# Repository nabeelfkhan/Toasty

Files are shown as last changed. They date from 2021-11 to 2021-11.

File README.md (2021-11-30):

# Toasty

Meet Toasty: The Brave Little Toaster Oven

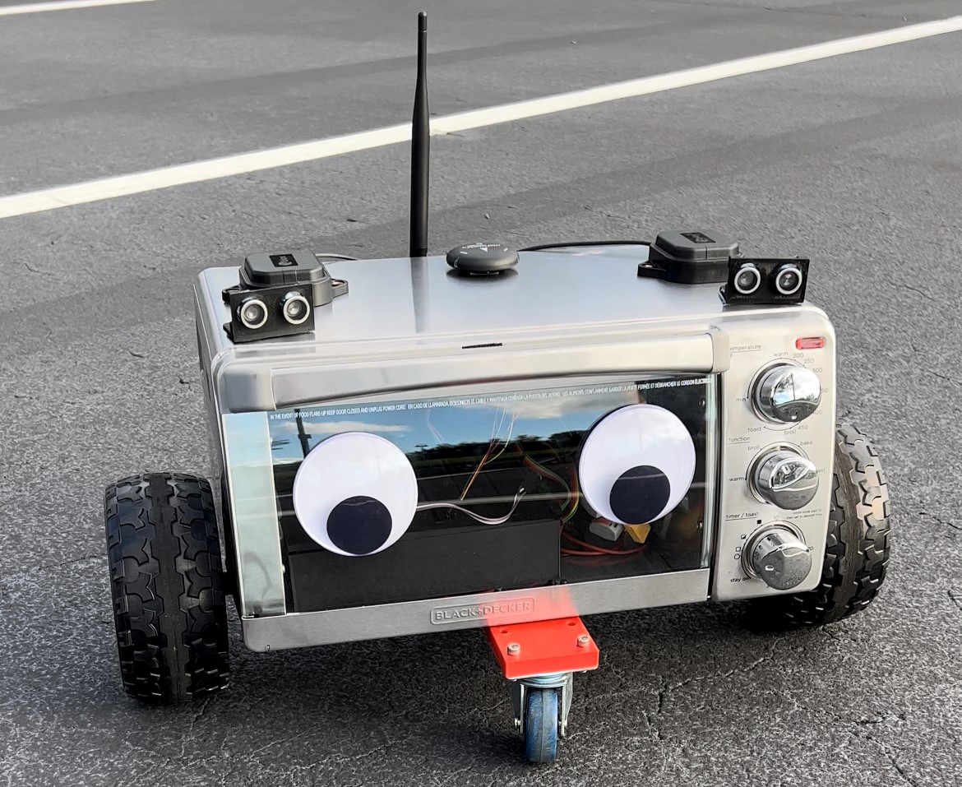
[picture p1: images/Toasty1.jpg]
Toasty
  
<p align="center">
  animated 
</p>

Toasty is an affordable DIY autonomous robotics research platform.  

**Disclaimer: The motors used in this project are dangerously powerful. Follow this guide at your own risk. Follow all local laws and regulations for autonomous and remote control vehicles. Test and make configuration changes in an open area away from obstacles, and always maintain line of sight.**

My long term goal is for Toasty to serve as a long range delivery robot with obstacle avoidance. In the near term, I'm experimenting wtith PointPerfect SSR GNSS corrections from u-blox to achieve cm level accuracy.

Pre-fabricated robotics platforms that can carry heavy loads over long distances are quite expensive. Cost effective Motors, Motor Controllers, and Frames are tough to find. Toasty is a budget and eco-friendly alternative, leveraging recycled materials and the following projects:

For brushless motor control, I referenced the excellent work of lucysrausch in hacking a hoverboard as a cost effective brushless motor solution.
Hoverboards are quite powerful. Most are capable of supporting 200 lbs (90kg) with a top speed of 25 mph (40km/h) and up to 10 miles (16 km) of range with some reprogramming.  
https://github.com/lucysrausch/hoverboard-firmware-hack  
Her repo also contains some examples of projects others have created using hacked hoverboards.  

EFeru further modified this code base to include FOC control, offering smoother control and higher speeds.  
https://github.com/EFeru/hoverboard-firmware-hack-FOC  

Randy Mackay's contributions to ArduRover made this project a breeze. Configuring Ardupilot for rover use is documented in detail on the official website.
Link to his YouTube channel with some tutorials:  
https://www.youtube.com/channel/UCm393BzMOyRPUo8MtKp5alg  

The best part of using these components is that minimal programming and configuration is needed to get started.

Hoverboards are out of style and sell for pennies on the dollar on ebay, craigslist, and facebook marketplace. I regularly find listings for $30 boards.
How can you beat a 10S Protected 4.4Ah 36V battery pack with a Charger, Battery Management System, two brushless 350W motors, and a frame capable of carrying 200lbs (90kg)?

The toaster oven is a sturdy aluminum enclosure that requires only basic tools to teardown and modify. You can find these used for $10-15. 
Aluminum extrusions just aren't as fun.

## Bill of Materials:

| Item  | Estimated Cost | Vendor
| --- | --- | --- |
| **Minimum BOM for RC control** |  | 
| Hoverboard | $20-60 | Plenty of used products on FB Marketplace, Craigslist, Ebay, etc.
| Toaster Oven |  $15 | Plenty of used products on FB Marketplace, Craigslist, Ebay, etc.
| Several 3D Printed mounts and enclosures (STL files included in repo) |  $5 | /3D_Prints
| 2x 2in Swivel Casters| $5 | https://www.harborfreight.com/material-handling/tires-casters/swivel-casters/2-inch-x-7-8-eighth-inch-light-duty-swivel-caster-41518.html  |
| RC Receiver for manual control and Arming (FS-iA6B)  | $12 | AliExpress, Amazon
| RC Controller or PS4 controller for manual control (FS-i6X)  | $40 | AliExpress, Amazon
| **Required for autonomous operation** |  |
| Ardupilot compatible flight controller w/ GNSS,Compass | $45-200+ | I used a Pixhawk 4 mini from Sparkfun. I can't vouch for the boards from AliExpress, but there are some lower cost options available. More options available here: https://ardupilot.org/rover/docs/common-autopilots.html#common-autopilotsSparkfun
| Telemetry Radio (BLE or SubGhz)  | $20 | Sparkfun, Amazon, Ebay
| **Optional for enhanced autonomous functions** |  |
| u-blox ZED-F9P/F9R High Precision GNSS Receiver (ZED-F9R also integrates Dead Reckoning)  | $150+ | Future, Digikey, Holybro, Ardusimple, Sparkfun
| Ultrasonic Sensors  | $10 | Sparkfun, Amazon, Ebay
| Cellular Modem for remote control  | $65+ | Sparkfun, Hologram
| Lidar or ToF camera  | TBD | TBD
| Raspberry Pi | $30 | https://www.raspberrypi.com/products/raspberry-pi-4-model-b/

## Block Diagram
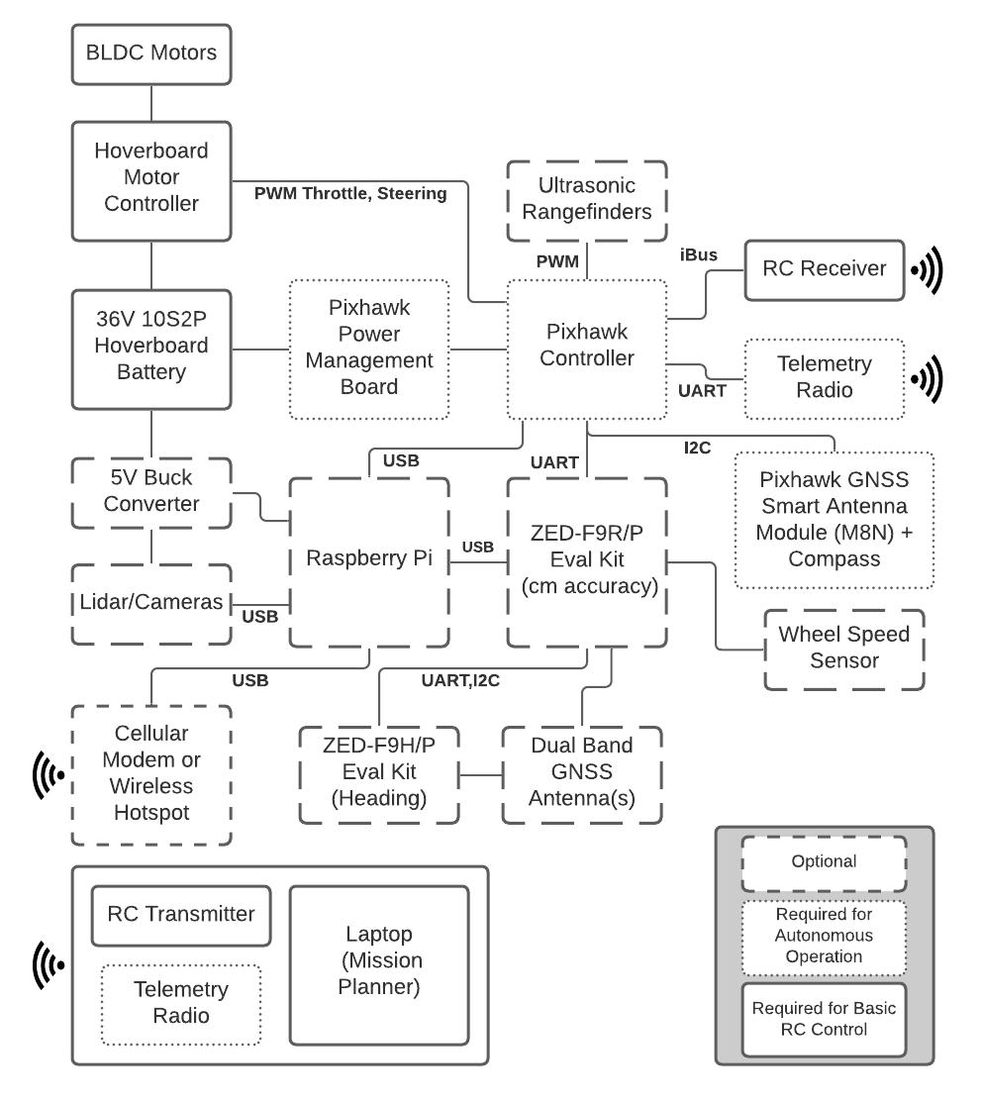
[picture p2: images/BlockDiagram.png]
Block Diagram
  

## Build

Here is an outline of the steps I followed using a Pixhawk 4 mini, Ardupilot,  and a hacked hoverboard. Depending on your choice of controller, you may need to make some modifications.

**Step 1**: Disassemble your hoverboard and Follow instructions on Feru's repo to flash the MCU. Make sure you pick the appropriate input. If you are using Ardupilot like me, select PWM input  
https://github.com/EFeru/hoverboard-firmware-hack-FOC  

**Step 2**: Mount the motors to the toaster frame. I used the mounts that came with my hoverboard, which required a couple 3D printed spacers. You may need to get a little creative here, as hoverboard mounts have different geometries and some may require more effort to combine with the toaster frame.
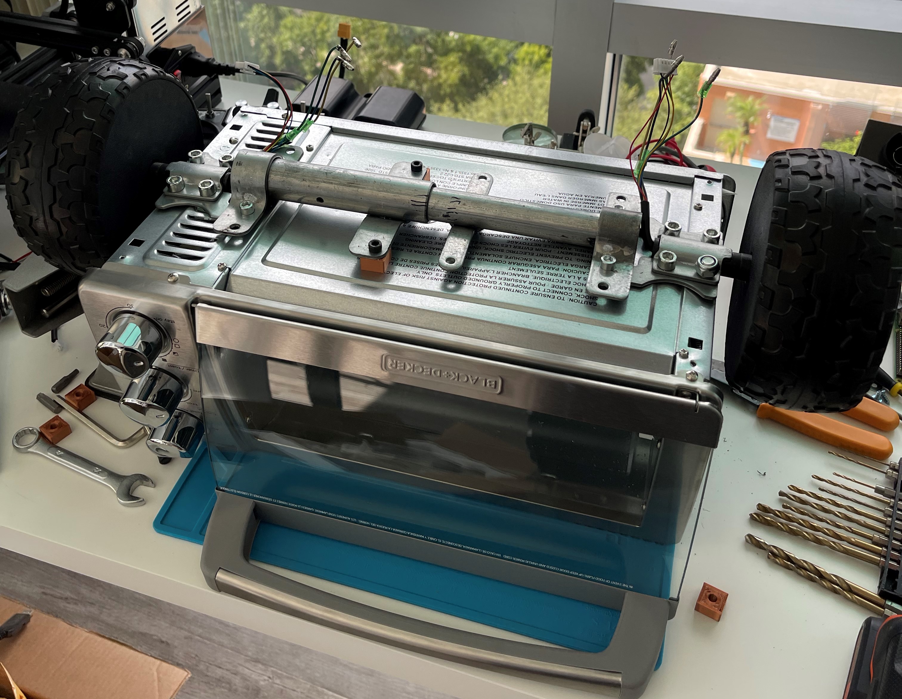
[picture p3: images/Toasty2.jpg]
Toasty
 

**Step 3**: Wire up the motor controller as shown in the block diagram. I 3D printed a few enclosures and mounts for the electronics. See /3D_Prints. I also crimped some custom dupont connector cables to interface between the motor controller and hall sensor cables.
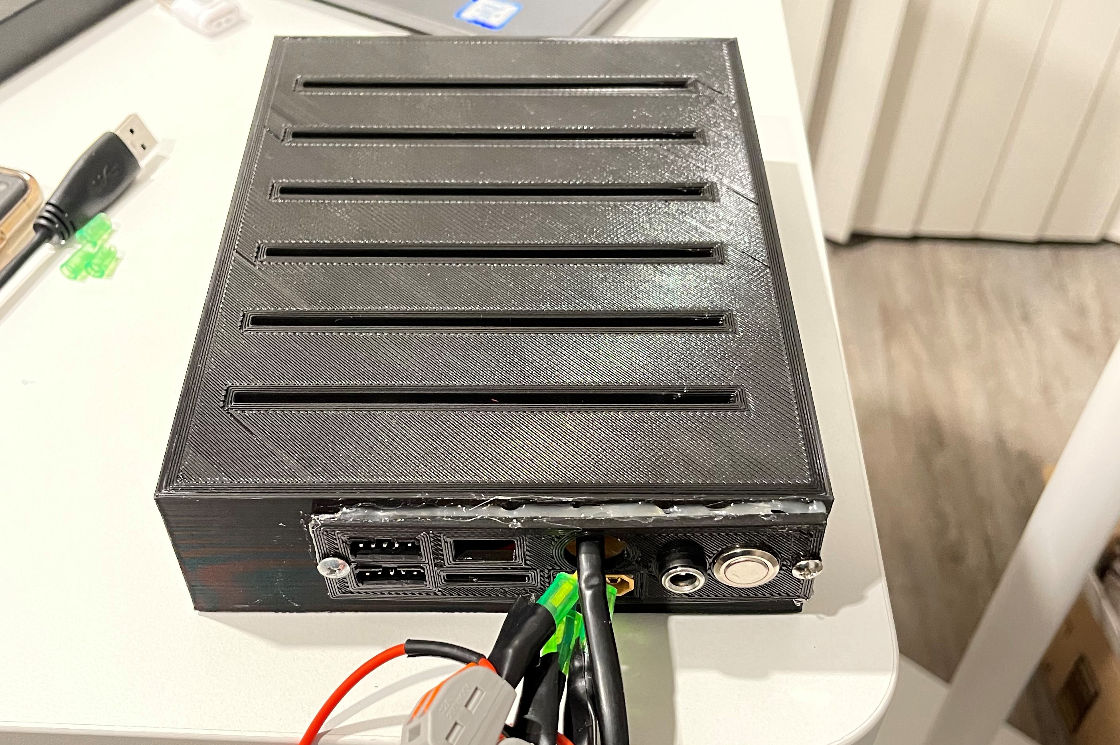
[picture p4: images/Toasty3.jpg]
Toasty
 

**Step 4**: Test with an RC receiver - Channels 0,1 can be connected directly to the hoverboard motor controller using Pin x for speed and pin x for steering. Place toasty on an elevated surface so the wheels can move freely and ensure throttle and steering are functioning as expected.
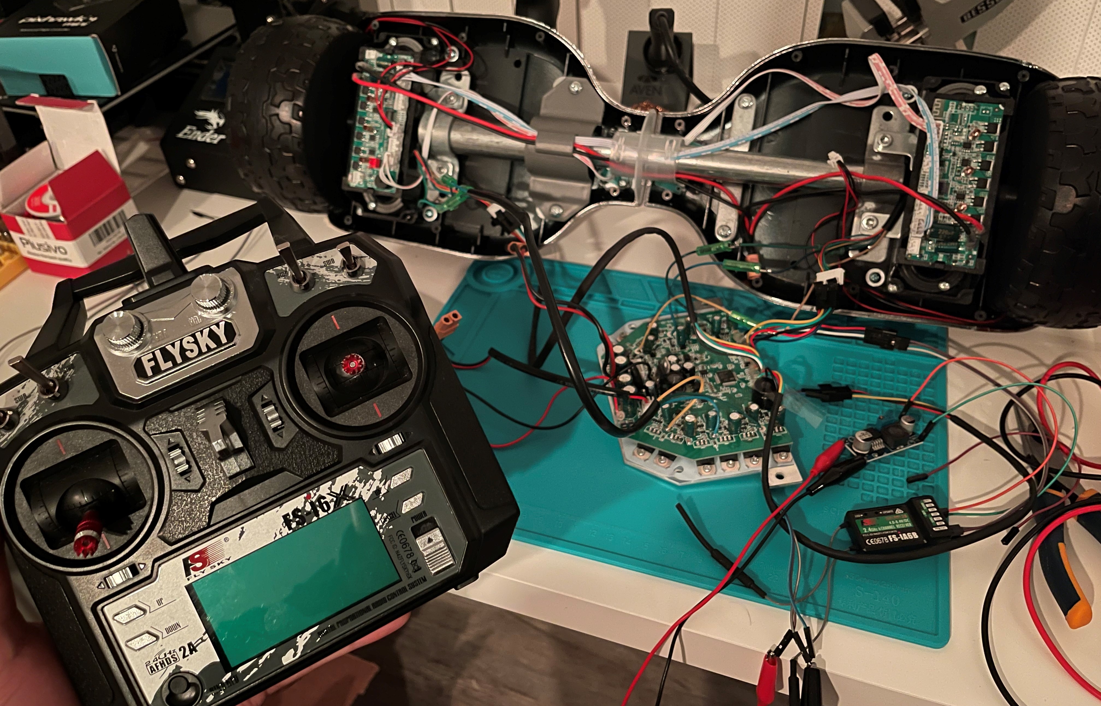
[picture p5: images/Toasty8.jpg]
Toasty
 

**Step 5**: Follow the Ardupoilot Rover steps outlined here: https://ardupilot.org/rover/docs/gettit.html  

**Step 6**: Connect the Pixhawk to the motor controller as shown on the block diagram. I've uploaded a 3D printed mount for the pixhawk in the repo. For convenience, I used velcro to secure the device to the top of the oven compartment.
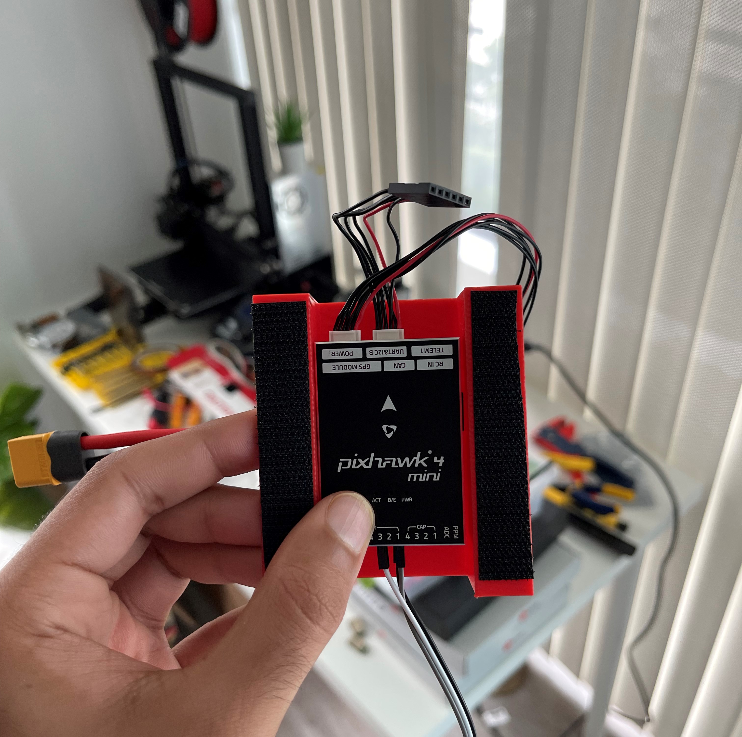
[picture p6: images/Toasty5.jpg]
Toasty
 
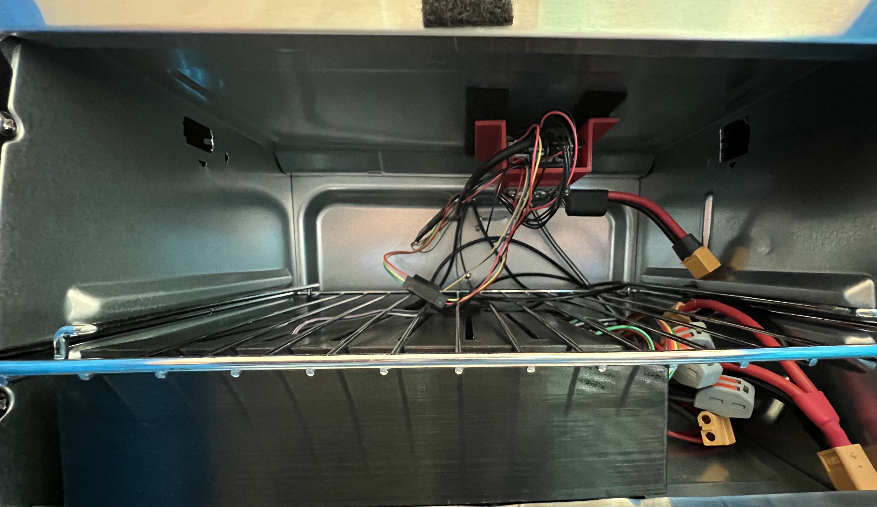
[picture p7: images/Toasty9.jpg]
Toasty
 

**Step 7**: Place Toasty on an elevated surface again to safely perform some motor tests. At this stage you should have already performed the RC controller calibration and set the rover to mode x. You're ready to go on your first mission!
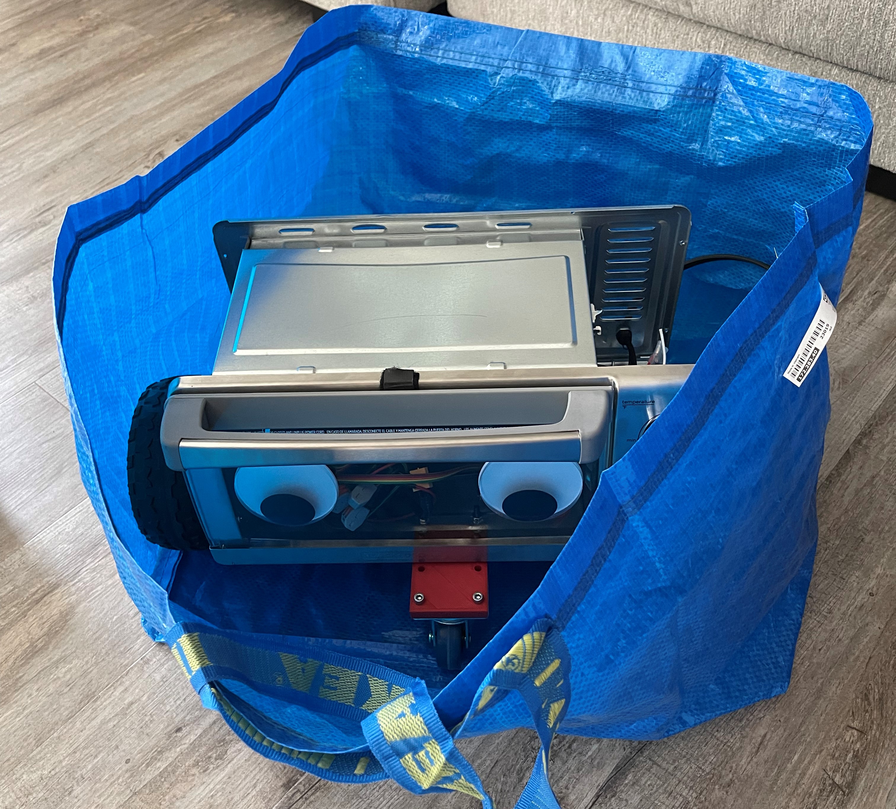
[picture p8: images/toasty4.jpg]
Toasty
 

**Step 8**: Test manual control and follow tuning steps as outlined in Randy's videos here:

https://www.youtube.com/watch?v=mV9Dxp1PX-8  
https://www.youtube.com/watch?v=9zOlvTsHY6k  

**Step 9**: Configure ardupilot to prioritize the appropriate external GNSS. Set up and calibrate magnetometers, and object avoidance sensors. Details are outlined in the ardupilot rover documentation: 

https://ardupilot.org/rover/docs/common-gps-for-yaw.html  
https://ardupilot.org/rover/docs/common-object-avoidance-landing-page.html  

Toasty 
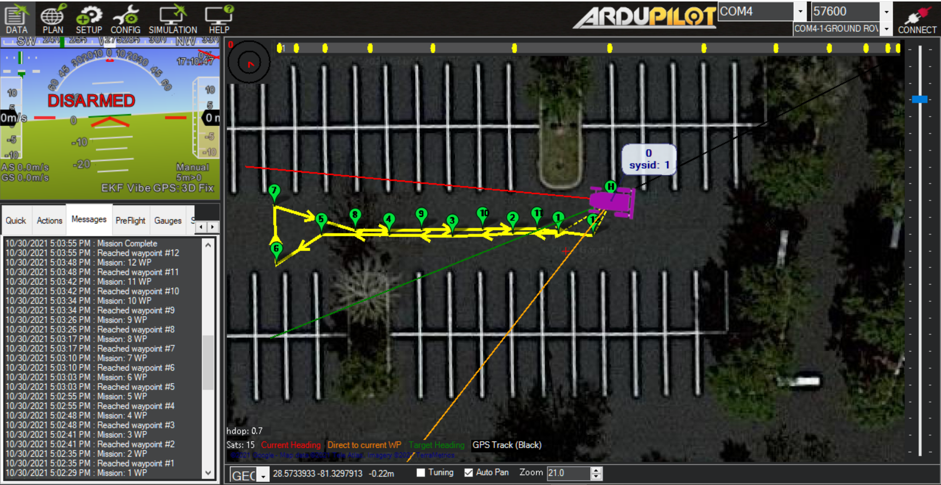
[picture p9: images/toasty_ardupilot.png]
Toasty
 

## Tips

- Configure maximum setpoints for throttle and steering if using Ardupilot. Toasty can and will spin out of control if you don't...

## To do:
Add obscacle avoidance via Lidar, ToF camera  
Include ROS node for indoor navigation.  
Migrate to Jetson Nano.  

## Links:
https://github.com/pixhawk/Hardware/blob/master/FMUv5/Pixhawk4-Pinouts.pdf  
https://www.thingiverse.com/thing:100486

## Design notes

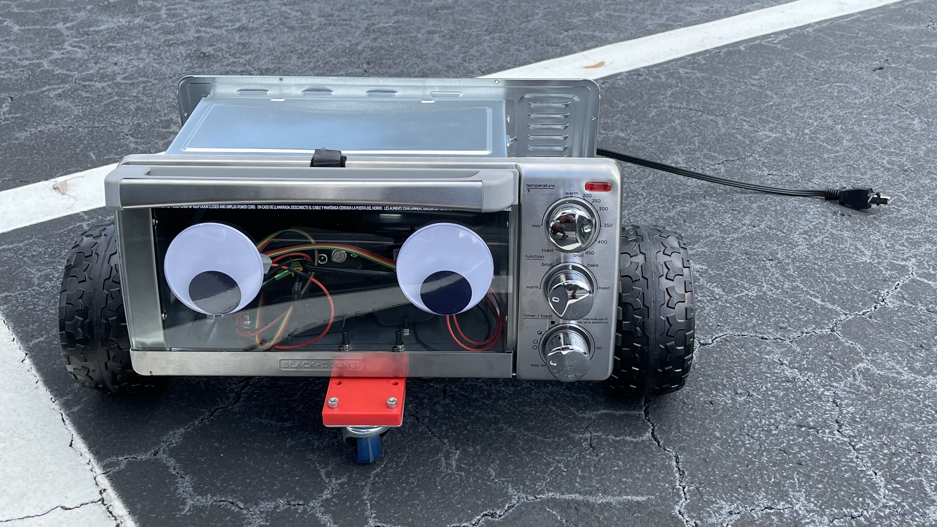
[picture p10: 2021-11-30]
images/toasty.jpg

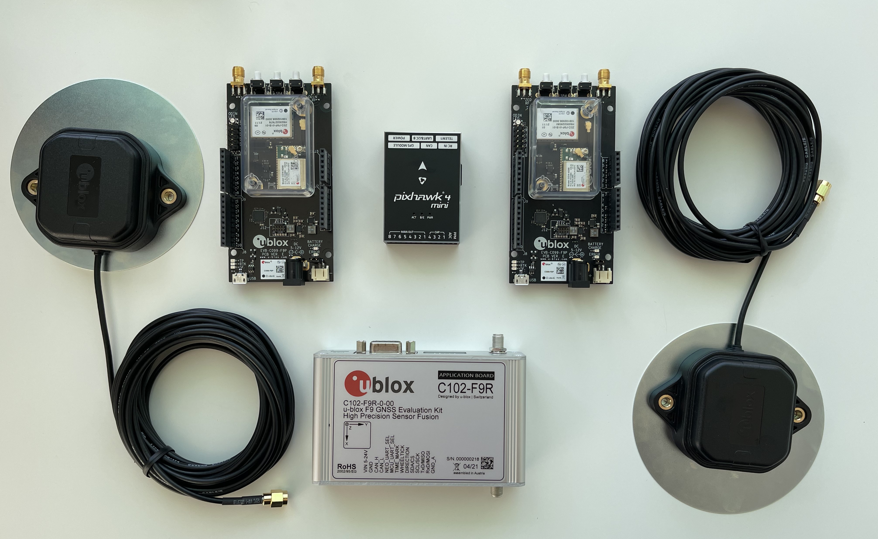
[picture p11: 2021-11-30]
images/Toasty7.jpg

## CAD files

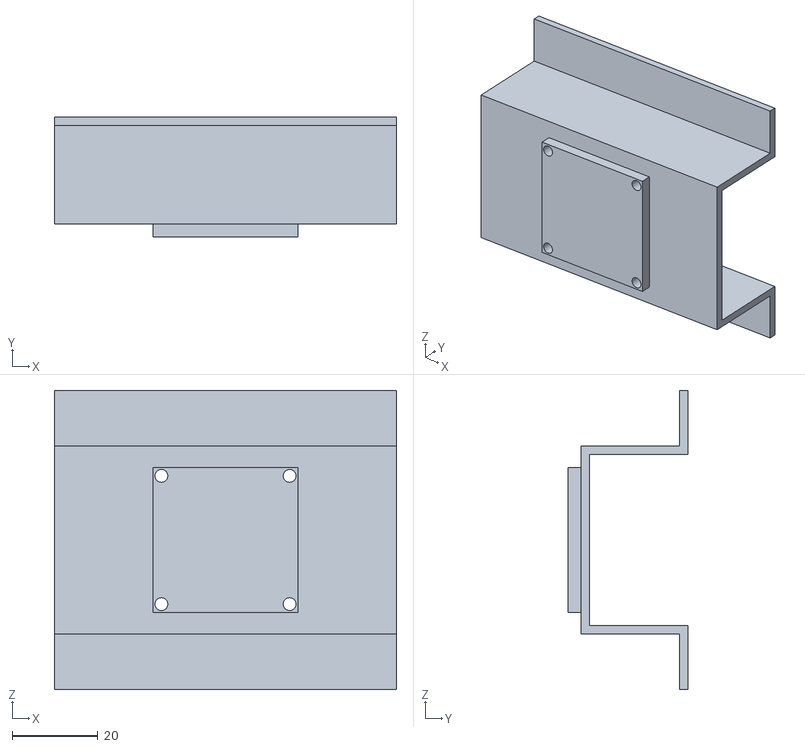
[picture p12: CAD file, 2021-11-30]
3D_Prints/px4holder.stl
80.0 x 28.0 x 70.0

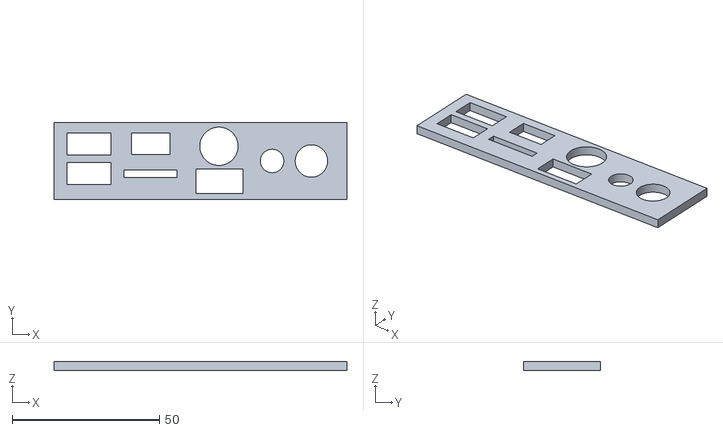
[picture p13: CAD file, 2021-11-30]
3D_Prints/esc_body_iopanel.stl
99.5 x 26.0 x 3.00

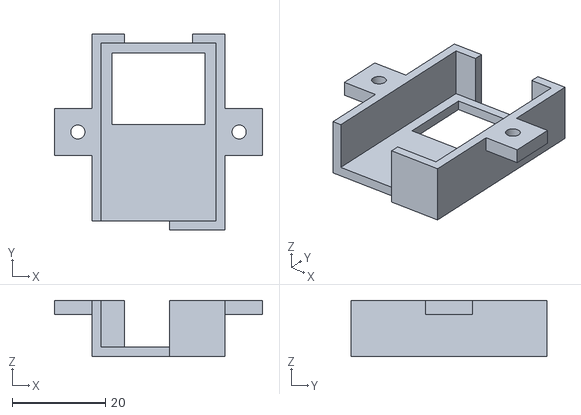
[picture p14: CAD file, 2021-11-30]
3D_Prints/900mhzradioholder.stl
44.5 x 42.0 x 12.0

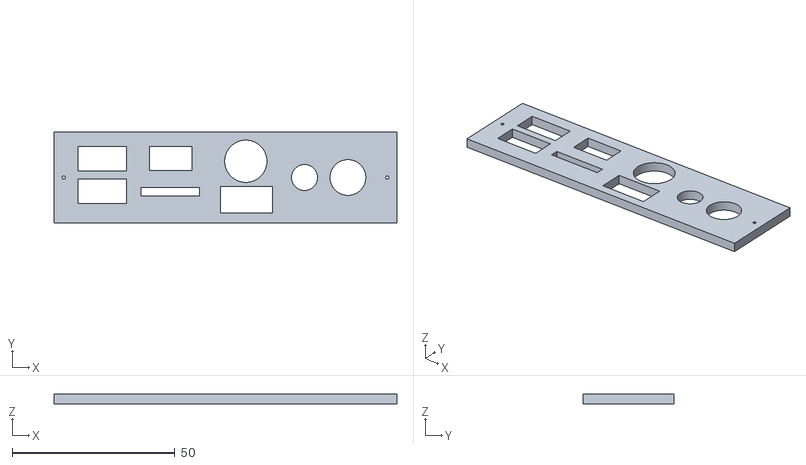
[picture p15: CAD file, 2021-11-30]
3D_Prints/esc_iocover.stl
105.5 x 28.0 x 3.00

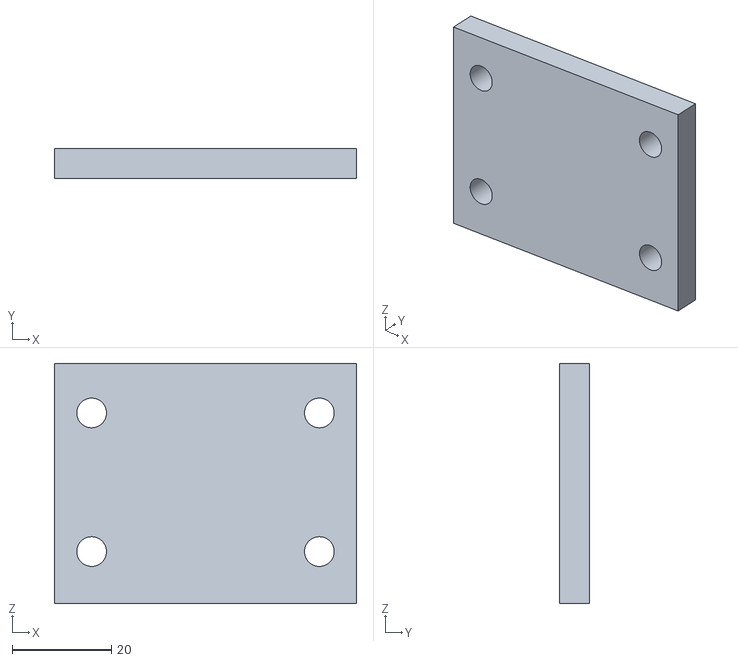
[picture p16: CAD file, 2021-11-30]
3D_Prints/wheel mount extension.stl
61.0 x 6.00 x 48.5

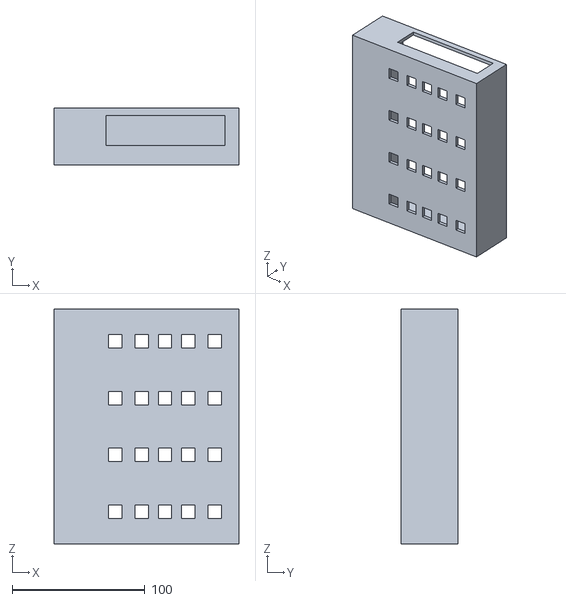
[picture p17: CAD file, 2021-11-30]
3D_Prints/esc_enclosure_body.stl
139.0 x 43.0 x 177.0
